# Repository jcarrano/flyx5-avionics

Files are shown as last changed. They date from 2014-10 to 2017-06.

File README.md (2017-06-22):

# FlyX5 Hardware #

This is the circuit board for the FlyX5 UAV controller.
See [here](https://github.com/jcarrano/flyx5-pilot) for the firmware that runs on the controller board.

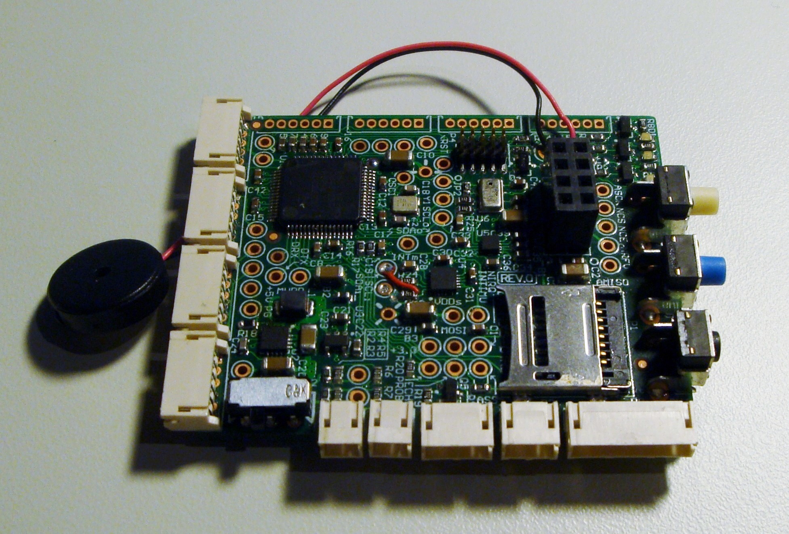
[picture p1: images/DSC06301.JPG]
FlyX5 Revision 0 Board Manufactured board


## Main board: flx_control ##

* Flight Stabilization and control.
* Tested. Works (except for errata listed below).

Features:

* Compact size: 54.5mm x 45.2mm
* Builtin buck converter: can be powered directly by batteries and provides 5V up to 1A.
* 3 Leds, 3 Buttons (2 programmable + reset).
* Microprocessor: TI Tiva-C (ARM M4F) with hardware floating point support.
* Supports up to 8 ESC. ESC ports can be configured as PWM or SPI.
* Radio-control port: 6 channels PWM input. Can be reconfigured as up to 3 duplex serial ports.
* Dedicated Serial Port.
* 2 Analog sense ports for battery sensing.
* Buzzer (with melodies)
* SD card slot.
* Expansion port (SPI+Power+2GPIO). Matches the pinout of a NRF2404+ module
* Gyro+Accelerometer: Invensense MPU-6500
* Magnetometer: Freescale MAG3110
* Altimeter: Freescale MPL3115A2
* Port for connecting ultrasonic ranger.

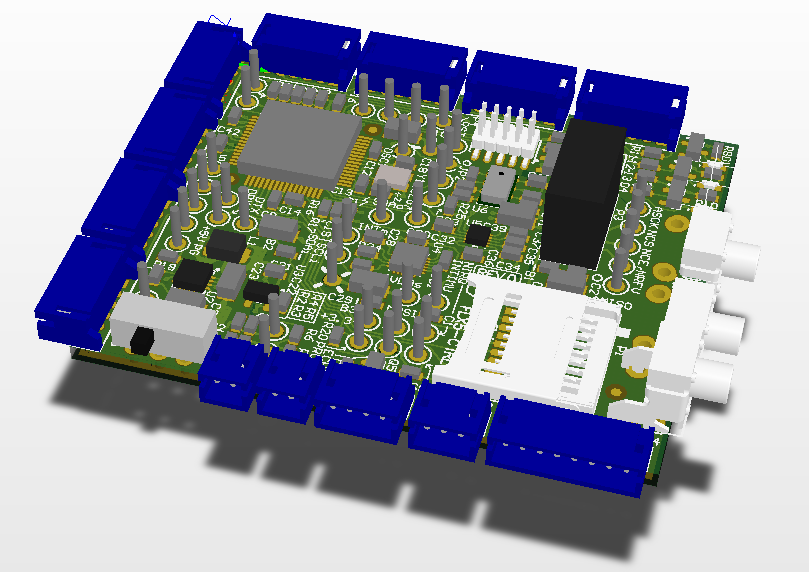
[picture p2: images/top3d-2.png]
3D rendering of PCB


Debugging and tinkering:

* JTAG port (can be programmed (and debugged) with a Tiva-C eval board and OpenOCD, no fancy HW required)
* Way too many testpoints.

### Errata ###

* On the first version, SDA and SCL lines for one I2C bus were reversed.
* The buzzer driver circuit is designed for magnetic buzzers. For piezo buzzers it requires a pull resistor. Newer versions should include a push-pull driver instead.
* The MCU has an errata, which has been worked around both in SW and HW.

## ESC controller board: flx_esc ##

SUPER experimental.

Features:

* Digital control via SPI: no more trimming/calibrating the PWM
* SPI allows reporting current motor speed (along with other parameters) back to control board.
* Uses a crystal for timing: no trimming or calibrating time.
* Processor: Kinetis KE02 (ARM M0+) allows for more advanced calculations (for example square root compensation for directly controlling thrust instead of speed)

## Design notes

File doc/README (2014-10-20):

Los PDFs (datasheets y app notes) van en el dropbox.

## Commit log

2014-03-27 Start project
    [FLXControl.PrjPCB, top_level.SchDoc]
2014-03-27 Create sheets.
    [FLXControl.PrjPCB, connectors.SchDoc, debug_and_interface.SchDoc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]
2014-03-31 Start schematic for DC/DC converter
    [FLXControl.PrjPCB, power.SchDoc]
2014-04-01 DC/DC schematic drawn. Designing MCU subsystem.
    [FLXControl.PrjPCB, mcu.SchDoc, power.SchDoc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]
2014-05-02 MCU connections
    [FLXControl.PrjPCB, connectors.SchDoc, debug_and_interface.SchDoc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]
2014-05-09 Trivial changes
    [connectors.SchDoc]
2014-05-09 Inverter prototype
    [Connectors.SchDoc, Inverter.PrjPCB, inv_schem.SchDoc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]
2014-05-11 Completed Schematic - Needs verification
    [FLXControl.PrjPCB, connectors.SchDoc, esc_connector.SchDoc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]
2014-08-06 Finished Schematics V0
    [FLX5.PcbDoc, FLXControl.PrjPCB, connectors.SchDoc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]
2014-08-06 resolve #18, resolve #17
    [FLX5.PcbDoc, FLXControl.PrjPCB, connectors.SchDoc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]
2014-09-02 Finish schematic Placed all components on pcb.
    [FLX5.PcbDoc, FLXControl.PrjPCB, connectors.SchDoc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]
2014-09-22 Terminado de rutear.
    [FLX5.PcbDoc, FLXControl.PrjPCB, debug_and_interface.SchDoc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]
2014-09-23 Terminado. Hay que revisar.
    [FLX5.PcbDoc, FLXControl.PrjPCB]
2014-09-23 Logo en el bottom layer.
    [FLX5.PcbDoc]
2014-10-12 Component placement on ESC board
    [CONECTORES.SchDoc, Connectors.SchDoc, ESC.PcbDoc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]
2014-10-19 Modifications on ESC board
    [ESC.PcbDoc, inverter.SchDoc, microcontroller.SchDoc]
2014-10-20 Finished FLX-CTRL
    [FLX5.PcbDoc, FLXControl.PrjPCB, debug_and_interface.SchDoc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]
2014-10-20 Fix sheet numbers.
    [FLX5.PcbDoc, FLXControl.PrjPCB, connectors.SchDoc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]
2014-10-21 remove via on pad rule.
    [FLX5.PcbDoc]
